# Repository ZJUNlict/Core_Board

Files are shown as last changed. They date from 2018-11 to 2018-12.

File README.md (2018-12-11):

# ZJUNlict Core Board Description
 
 The core board contains the minimum system for an Alter FPGA ([Cyclone III EP3C25](https://www.intel.com/content/www/us/en/products/programmable/fpga/cyclone-iii.html)). (The board is designed using [Altium Designer](https://www.altium.com/altium-designer/) 17.1)

The 2D and 3D design views are shown below:

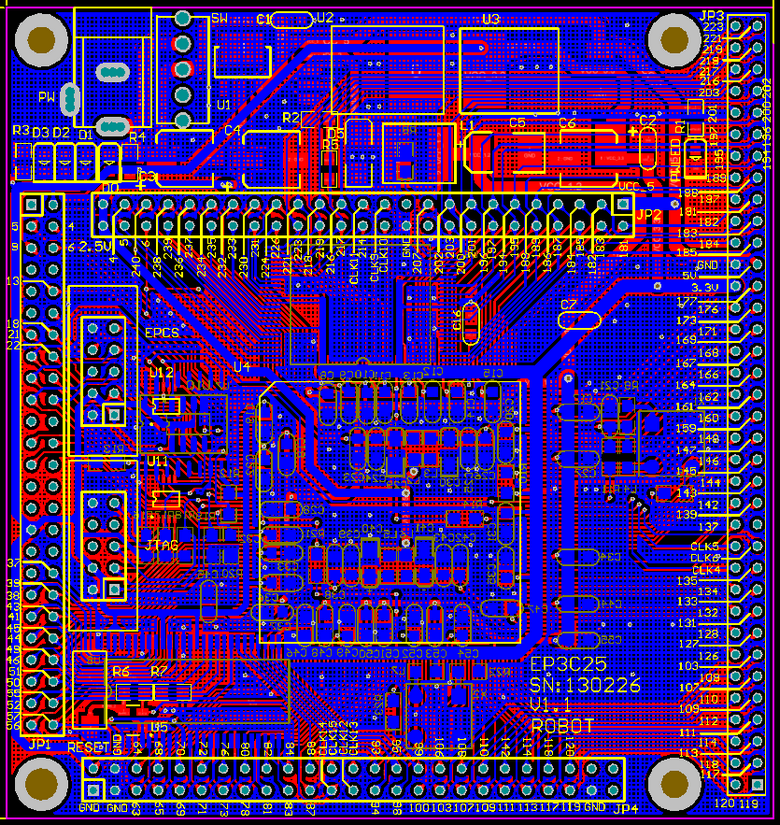
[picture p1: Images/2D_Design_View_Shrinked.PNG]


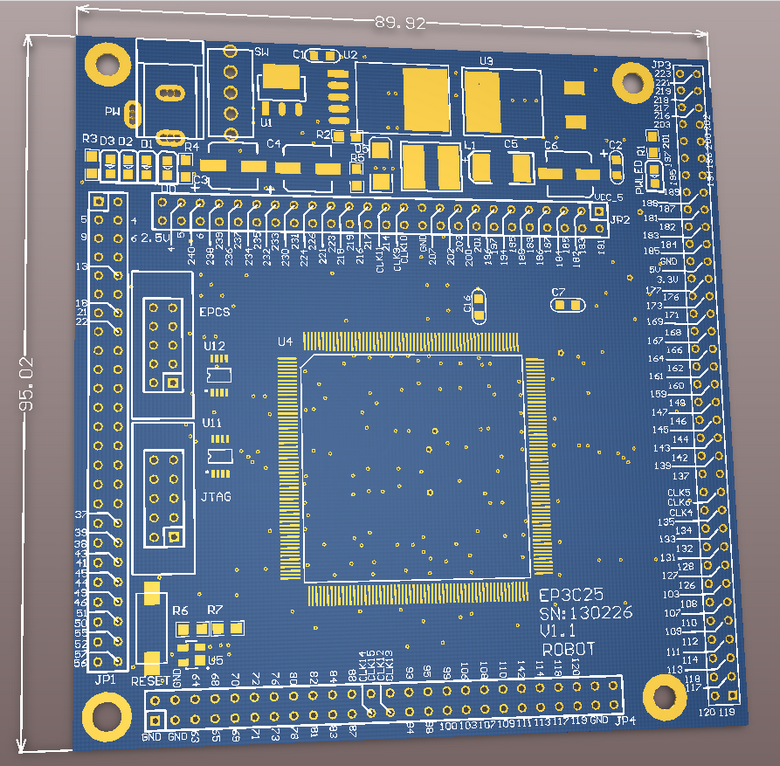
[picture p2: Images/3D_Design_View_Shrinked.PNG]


The main features are:

* Altera EP3C25Q240 FPGA IC as the main chip controls the robot. The firmware can be found in [its repository](https://github.com/ZJUNlict/Firmware_for_Core_Board).
* External 64Mbit SDRAM (HY57V641620) as the memory for Nios II processor created in FPGA.
* External 64Mbit Flash (JS28F640) as the flash for storage.
* 4LEDs indicate hall sensor failure of each driving motor.

The photos of the core board are shown below as references. 

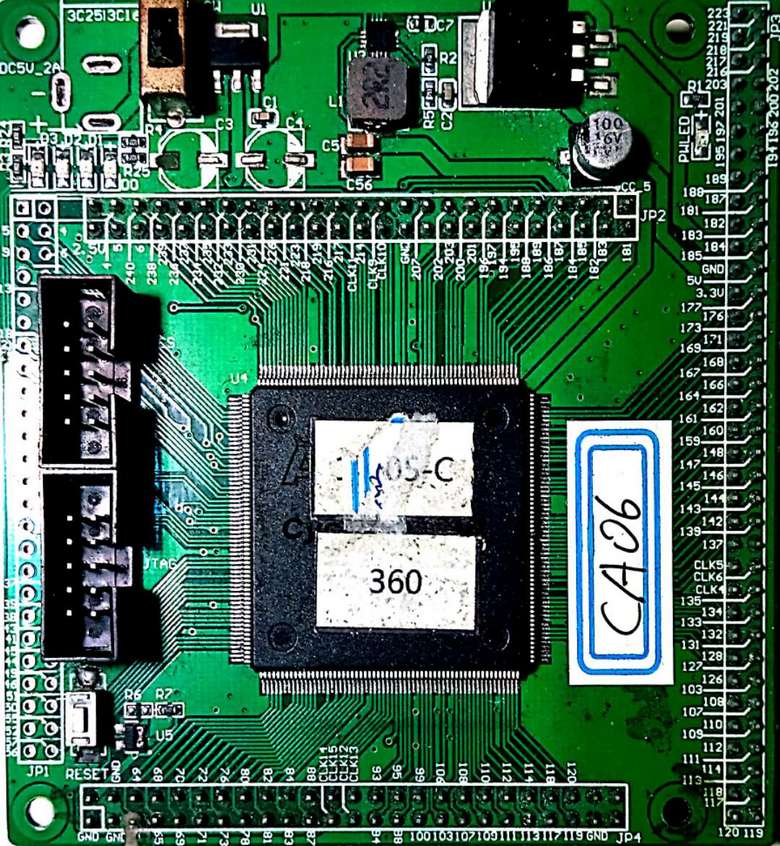
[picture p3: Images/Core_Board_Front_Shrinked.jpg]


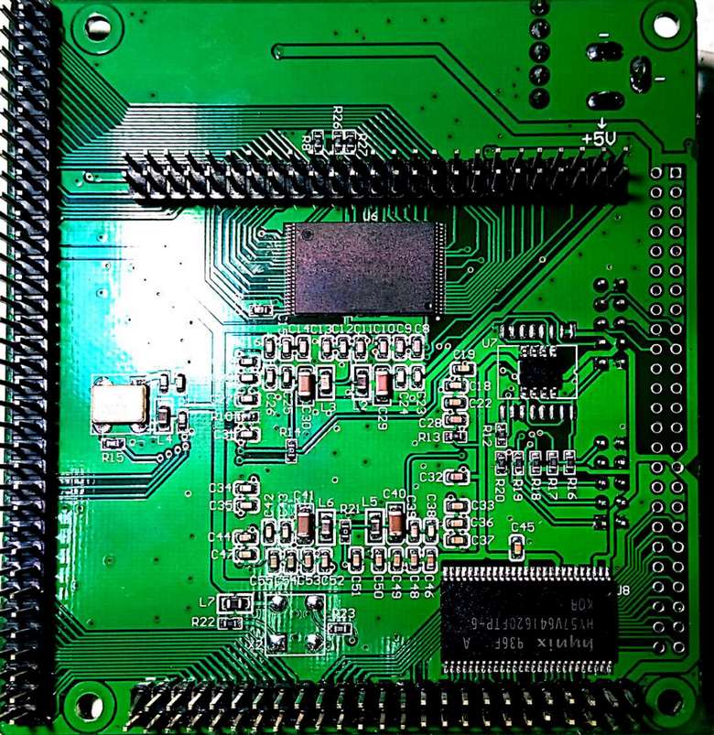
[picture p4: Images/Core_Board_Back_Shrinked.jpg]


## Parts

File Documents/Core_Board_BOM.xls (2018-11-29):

BOM List
 | Name | Spec | Package | Quantity | Pos | Remark
 | Cap | 0.1uF | 0805C | 43 | C1, C2, C7, C8, C9, C10, C11, C12, C13, C14, C15, C16, C17, C18, C19, C20, C21, C22, C24, C26, C27, C28, C31, C32, C33, C34, C35, C36, C37, C39, C43, C44, C45, C46, C47, C48, C49, C50, C51, C52, C53, C54, C55
 | Cap | 220uF | Cap6.6*6.6 | 1 | C3
 | Cap | 100uF | Cap6.6*6.6 | 2 | C4, C6
 | Cap | 220uF | 8228 | 1 | C5
 | Cap | 0.001uF | 0805C | 4 | C23, C25, C38, C42
 | Cap | 10uF | 3216C/A | 4 | C29, C30, C40, C41
 | LED | LED0 | 0805A | 1 | D0
 | LED | LED1 | 0805A | 1 | D1
 | LED | LED2 | 0805A | 1 | D2
 | LED | LED3 | 0805A | 1 | D3
 | Diode | S340 | SMB | 1 | D5
 | IC | EPCS | 302S-10P | 1 | EPCS
 | Connector | Bank1 | 201S-3C-2*25PG-6.0/3.0 | 1 | JP1
 | Connector | Bank2 | 201S-3C-2*25PG-6.0/3.0 | 1 | JP2
 | Connector | Header 36X2 | 201S-3C-2*36PG-6.0/3.0 | 1 | JP3
 | Connector | Bank4 | 201S-3C-2*25PG-6.0/3.0 | 1 | JP4
 | Connector | JTAG | 302S-10P | 1 | JTAG
 | Inductance | 47uH | 功率贴装 | 1 | L1
 | Inductance | 600 Ohm@100Mhz | 0805R | 6 | L2, L3, L4, L5, L6, L7
 | Connector | CON3 | PW_PORT | 1 | PW
 | Diode | LED | 0805A | 1 | PWLED
 | Resistor | 1K | 0805R | 3 | R1, R3, R4
 | Resistor | NC | 0805R | 2 | R2, R6
 | Resistor | 0 | 0805R | 3 | R5, R14, R21
 | Resistor | 4.7K | 0805R | 1 | R7
 | Resistor | 5.1K | 0805R | 1 | R8
 | Resistor | 10K | 0805R | 11 | R9, R10, R11, R12, R13, R16, R17, R18, R19, R20, R22
 | Resistor | 33 | 0805R | 2 | R15, R23
 | Connector | SW-PB | SMD_SWITH | 1 | RESET
 | Connector | SW SPDT | PW_SW | 1 | SW
 | IC | 1117-2.5 | SOT-223 | 1 | U1
 | IC | LM2596 | LM2596_TO263 | 1 | U2
 | IC | AMS1084_33 | AMS1084-ADJ | 1 | U3
 | IC | EP3C25 | PQFP240 | 1 | U4
 | IC | MAX811T | SOT143 | 1 | U5
 | IC | JS28F640 | SOP56_E28F640 | 1 | U6
 | IC | EPCS16 | SOP16_EPCS16 | 1 | U7 | or use U10
 | IC | HY57V641620 | TSOP54 | 1 | U8
 | IC | EPCS16 | so8 | 1 | U10 | or use U7
 | IC | PACDN046M | MSOP8 | 2 | U11, U12
 | IC | CLOCK_SOURCE | CRYSTAL4 | 2 | X1, X2

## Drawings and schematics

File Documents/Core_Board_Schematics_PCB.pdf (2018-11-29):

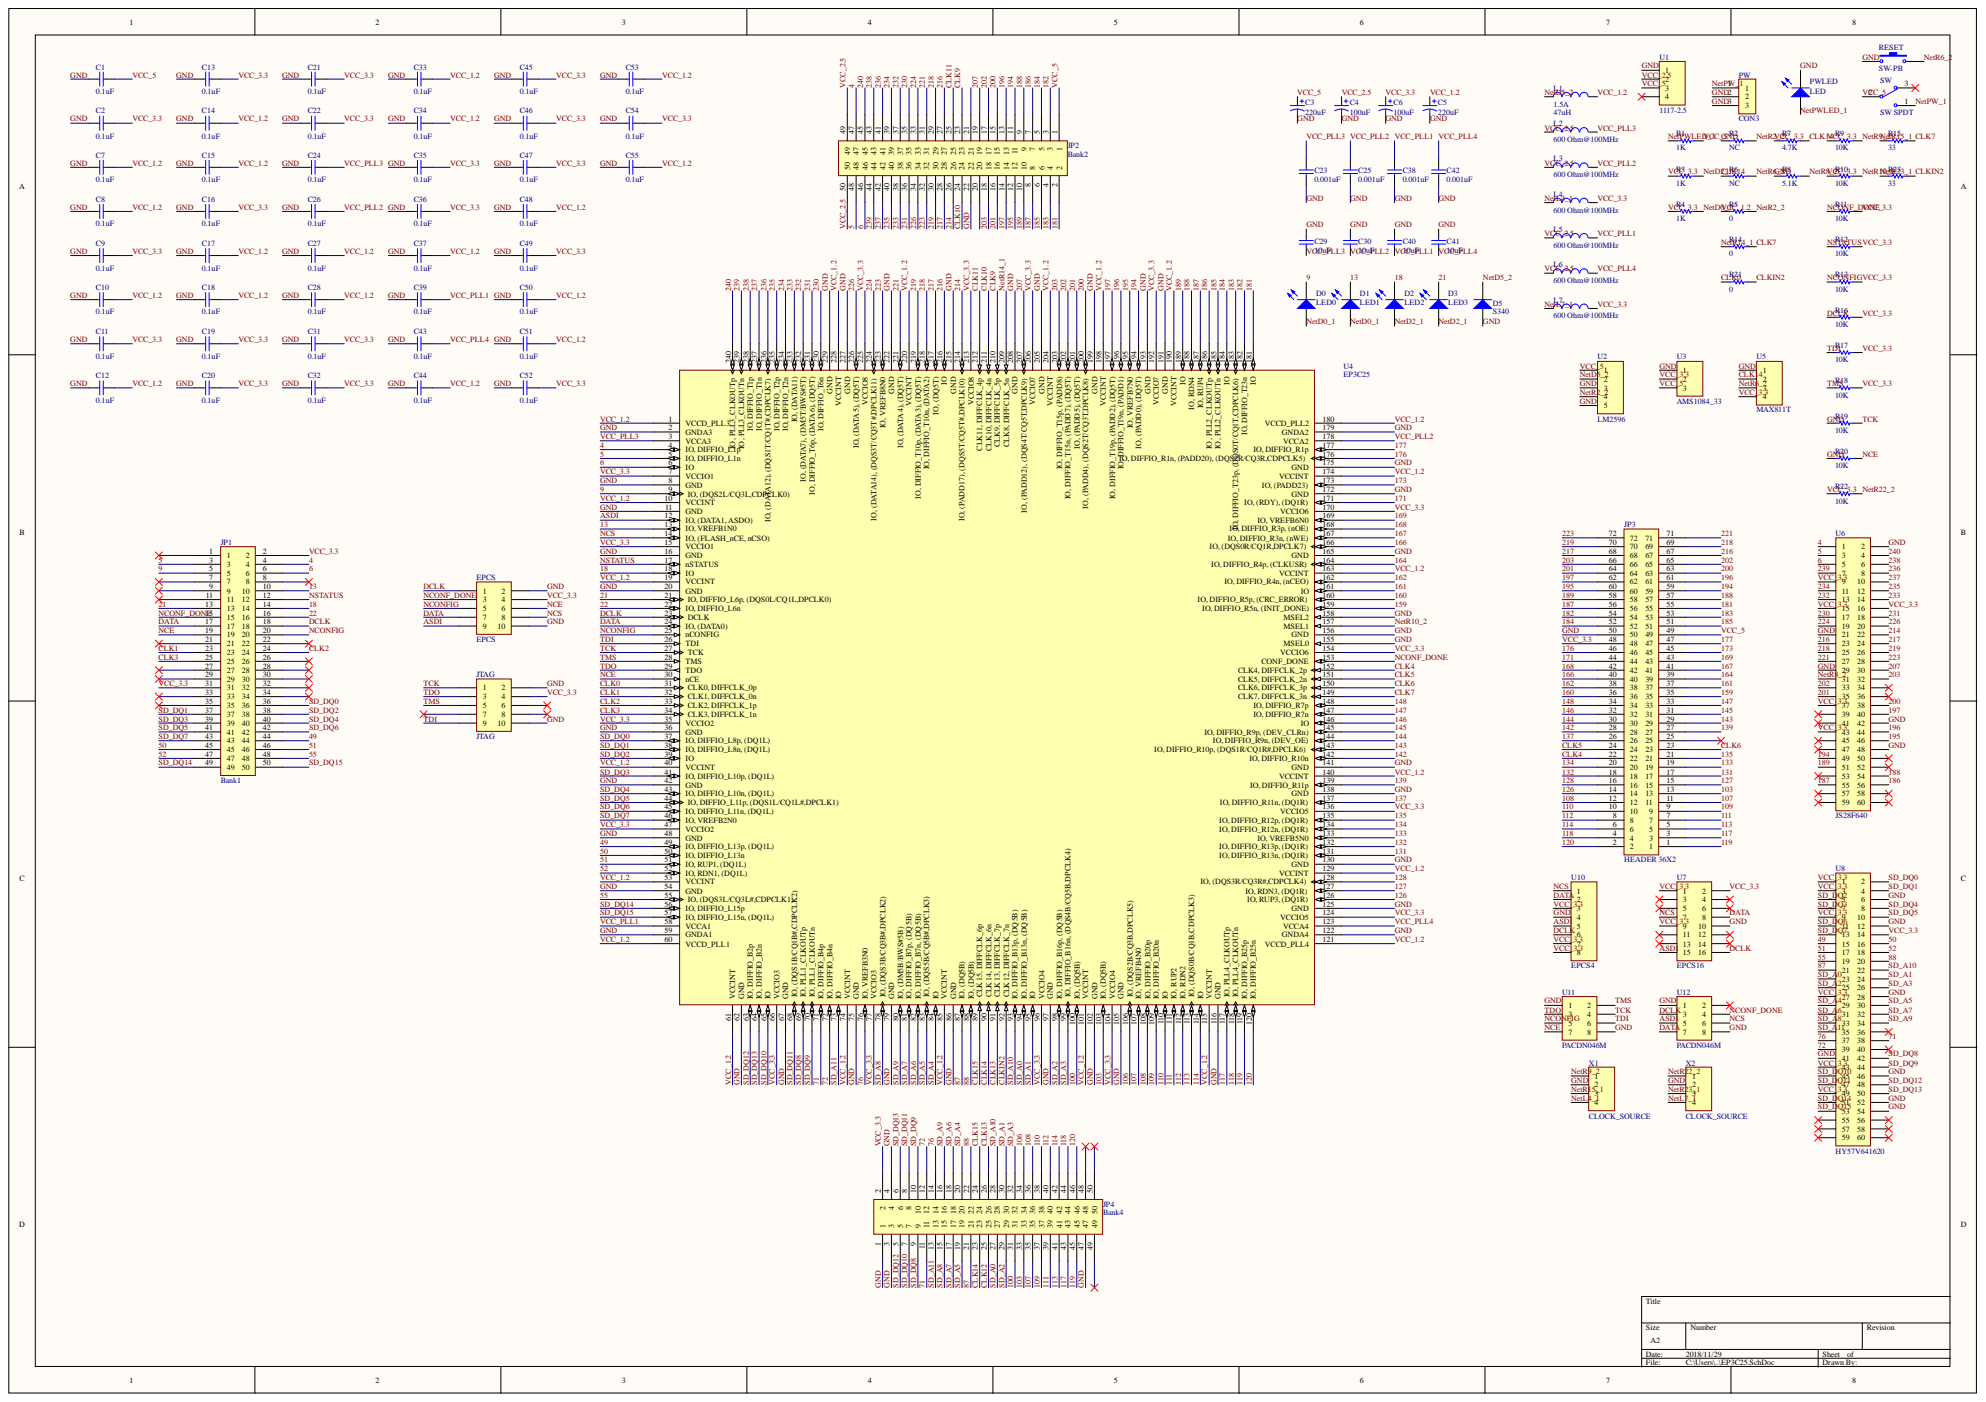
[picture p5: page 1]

IO, DIFFIO_T6n 230 IO, DIFFIO_T6p, (DATA6), (DQ5T) 231 IO, (DATA7), (DM5T/BWS#5T) 232 IO, (DATA11) 233 IO, DIFFIO_T2n 234 IO, DIFFIO_T2p 235 IO, (DATA12), (DQS1T/CQ1T#,CDPCLK7) 236 IO, DIFFIO_T1n 237 IO, DIFFIO_T1p 238 IO, PLL3_CLKOUTn 239 IO, PLL3_CLKOUTp 240

IO 216 IO, (DQ5T) 217 IO, DIFFIO_T10n, (DATA2) 218 IO, DIFFIO_T10p, (DATA3), (DQ5T) 219

IO, (PADD4), (DQS2T/CQ3T,DPCLK8) 200 IO, (PADD5), (DQ5T) 201 IO, DIFFIO_T15n, (PADD7), (DQ5T) 202 IO, DIFFIO_T15p, (PADD8) 203

IO, (PADD0), (DQ5T) 194 IO, VREFB7N0 195 IO, DIFFIO_T19n, (PADD1) 196 IO, DIFFIO_T19p, (PADD2), (DQ5T) 197

IO 181 IO, DIFFIO_T23n 182 IO, DIFFIO_T23p, (DQS0T/CQ1T,CDPCLK6) 183 IO 184 IO, PLL2_CLKOUTn 185 IO, PLL2_CLKOUTp 186 IO, RUP4 187 IO, RDN4 188 IO 189

TDI TCK TMS TDO

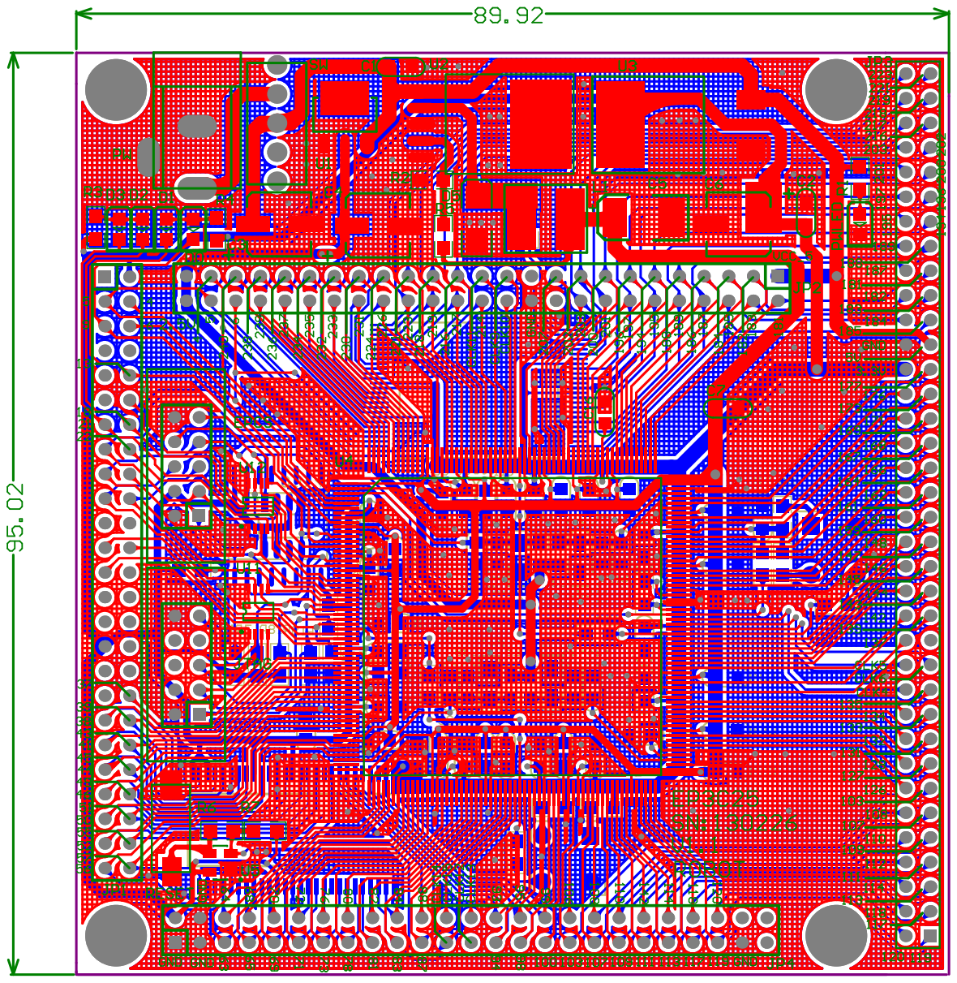
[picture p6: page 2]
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

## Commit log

2018-11-19 Add PCB files
    [EP3C25.PcbDoc, EP3C25.PcbLib, EP3C25.SchDoc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]
2018-11-29 Add Readme and modify BOM list
    [Core_Board_BOM.xls, 核心板元器件清单.xls]
